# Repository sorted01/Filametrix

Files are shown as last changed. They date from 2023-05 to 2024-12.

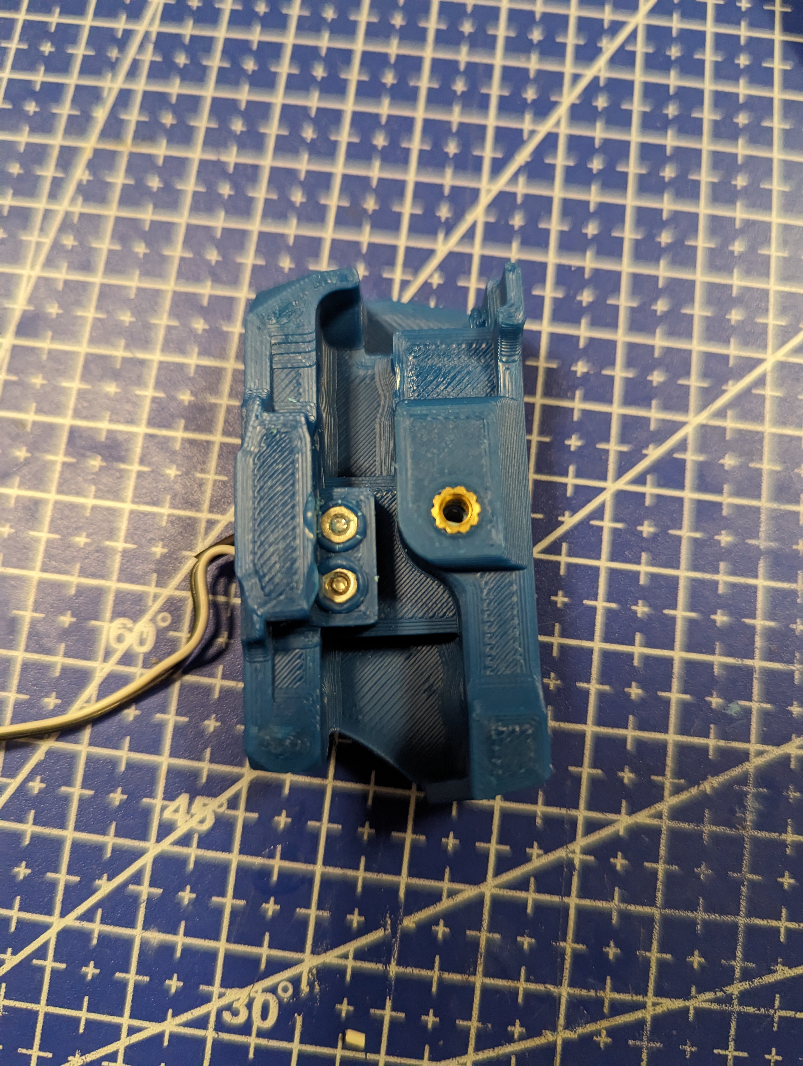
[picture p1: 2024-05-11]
STL/StealthOrbiter/PXL_20240206_062519943.jpg

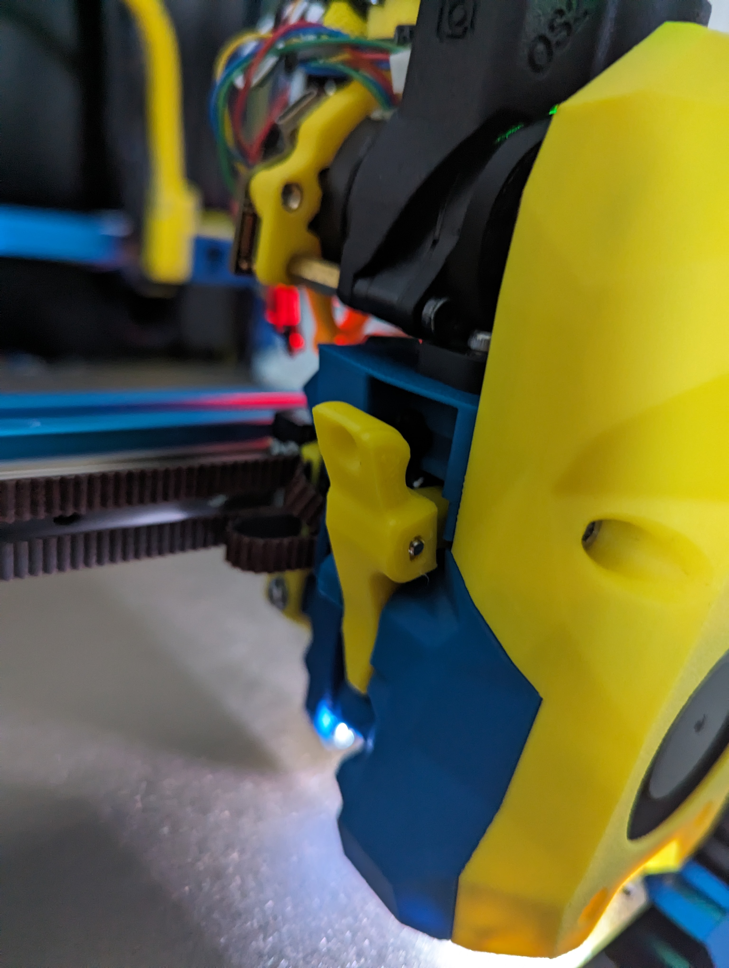
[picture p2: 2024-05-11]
STL/StealthOrbiter/PXL_20240206_194107226.jpg

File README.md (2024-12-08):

# Filametrix Mod


This is a mod of the Voron Stealthburner which adds a filament cutting possibility!




### Main Body
#### Main Body for old motor plate of Clockwork2
- SB_CW2_Main_Body_Cutting_with_2xD2F_ECAS
- SB_CW2_Main_Body_Cutting_with_D2F_ECAS
- SB_CS2_Main_Body_EBB_ECAS_D2F "CW2 main body for the ERCF w/ ECAs, bearing switch, and SB2209 Canbus mods" Thanks to [juliusjj25](https://github.com/juliusjj25)

#### Main Body for new motor plate of Clockwork2
Adapting to recent changes in the Clockwork2 design (July 2023) - Left new / Right old
grafik

A step with file the material removed of the motor plate is available here [Cutoff new motor plate](https://github.com/sorted01/Filametrix/blob/main/CAD/CW2_new_motor_plate/SB_CW2_cutoff_new_motor_plate.stp)

*Not all main bodys are converted yet. Use the old [motor plate](https://github.com/sorted01/Filametrix/blob/main/STL/motor_plate.stl) if your main body is not listed below.*

A more compact version using a M6 bowden fitting instead of the ECAS is also available for some main bodys. 
Additonally, a more rigid [latch](https://github.com/sorted01/Filametrix/blob/main/STL/[a]_latch_M6.stl) is available for the M6 version. (ECAS version of the latch is compatible with all M6 main bodys.)

* ECAS mount
	- SB_CW2_new_motor_plate_Main_Buddy_Cutting_with_ECAS

* M6 bowden mount
	- SB_CW2_new_motor_plate_Main_Buddy_Cutting_with_M6

#### Support for LGX Lite
https://www.printables.com/de/model/576122-lgx-lite-stealthburner-filament-cutter

tommorox234 has created the main body for the LGX Lite. Feel free to get in contact with him via printables.
Thank you :)

#### Support for StealthOrbiter
- ORBITERMOUNT_STANDARD_PG7_V2_Cutting

by [emjay276](https://github.com/emjay276)

### Printhead
#### Update for Phaetus Dragon UHF and Phaetus Dragon UHF mini
- SB_Dragon_UHF_cutting_TH_Front or SB_Dragon_UHF_mini_cutting_TH_Front
- SB_Dragon_UHF_cutting_TH_Rear or SB_Dragon_UHF_mini_cutting_TH_Rear
- Knife_holder_Dragon_UHF

by [emjay276](https://github.com/emjay276)

#### Update for Bambu Hotend has been added.
- SB_Bambu_cutting_Printhead_back
- SB_Bambu_cutting_Printhead_front or SB_Bambu_cutting_Printhead_front_2
- Bambu_Adapter

Thanks to "Jakub Kadlec" from Facebook :) 

#### Update for Voron Revo Hotend 
- SB_RevoVoron_back
- SB_RevoVoron_front

by Russell Gower - NOTE currently untested!!

#### Update for Rapido Hotend

- see folder

say thank you to [juliusjj25](https://github.com/juliusjj25)  :) 

#### Update for Slice engingeering mosquito hotend

https://www.printables.com/de/model/614813-filametrix-mod-for-slice-engingeering-mosquito-hot

say thank you to "https://www.printables.com/de/@MakeAUsername_285162"

#### Update for Revo Micro
- SB_RevoMicro_back
- SB_RevoMicro_front

by Leif Lang - NOTE: Remixed from the Official Stealthburner and the remixed version for the Revo Voron by Russel Gower

## Motivation
I was looking at the ERCF MMU for several month now. What always kept me from starting the project were the discussions about issues and problems with  filament tip forming. Suddenly a new company showed us how they do it quite reliable. They just cut the filament. Further motivated and inspired by the design of @pure100kim who has built the [ERCF_Filament_Cutting_MOD](https://github.com/pure100kim/ERCF_Filament_Cutting_MOD) I started to build my own version of it.

## See how it works

Proof of concept 1: https://youtube.com/shorts/HOMG8cVk_U4

Proof of concept 2: https://youtu.be/tTcrxttyths

Filametrix in action: https://www.youtube.com/watch?v=tfMZWQRqtvY

## Good to know

Please be aware:
- We will need to use one of the ADXL mounting threads
- Depending on the setup and position of the cutting point we will most probably not lose any build volume
- For the main body i remixed the ECAS version from [Alexanderor](https://www.printables.com/de/model/433797-clockwork-2-ecas-fitting-for-ercf)

## What you need
### Print list
#### Toolhead
- 1x SB (hotend name) cutting Printhead back
- 1x SB (hotend name) cutting Printhead front
- 1x SB Main body Cutting with ECAS (or with sensor)
- 1x SB motor plate (as Stealthburner has seen a small update the newest plate does not fit anymore. So please use the one from this git)
- 1x SB latch ECAS
- 1x Cutting arm
- 1x Knife holder

#### Cutting point on gantry
- 1x depressor mount
- 1x depressor

#### Cutting point on gantry with servo
- tbd...

### Parts list - considering you already have a Stealthburner with Dragon Hotend

#### Toolhead: 
- Loctite
- 1x M3 nut (DIN934; ideally a countersunk tool to modify the nut for proper filament insertion)
- 2x M3 washer (0.5mm)
- 1x M3x18 SHCS (it repleaces the top left M3x25 SHCS from the SB-Cover mount) 
- 2x Voron heat inserts
- 1x M3x18 FHCS (counter sunk screw)
- 1x M3x8 SHCS
- 1x M2.5x16 SHCS (15-18mm works)
- Spring 0.4x4x15 or alternative of ballpoint pen (L=15mm; D<=4,5mm) (I've ordered some for testing, to have a "defined" spring)
- Type 4 metal hobby blades (we will cut it to length) [Link](https://de.aliexpress.com/item/1005005117830095.html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) Amazon link, these need glue to be held in but work fine (USA) [Link](https://www.amazon.com/dp/B07QP8L1QG)
- 

#### Cutting point on gantry
- 1x M3x16 BHCS
- 1x M3 nut
- 1x M3x8 FHCS
- 2x M3 SHCS (Lengths: 6mm - no backers, 10mm - titanium backers, 12mm - MGN9 rails)
- 2x Voron heat inserts

## Assembly
### Cutting arm
#### Cut skalpel to length l=26mm

##### Result

#### Insert skalpel into knife holder
Insert the skalpel (which is cut to 26mm) into the knife holder until you see it in the little hole. Use pliers to push it into the knife holder. Some force should be needed as the skalpel should stay in place due to the "pressfit". If that's not the case add some glue.(Depelding on skalpel tolerances)

#### Put knife holder into cutting arm
The M2.5x15 screw is directly screwed into the plastic of the knife holder. The tip of the screw should be flush with the cutting arm or no more than 0.1-0.3mm above it.
Check the orientation of the hole for the M2.5 screw in the knife holder. It needs to be on the bottom side.

**!! The knife holder must move up and down without friction in the cutting arm but shoult not have a lot play. Maybe some grinding is needed. !!**




### Add heat inserts

Tip here for the heat set that goes above the cutter I would suggest drilling the threads out with a ~2.5mm drill bit. On the hotend holder side below the cutter make sure you flare out the PTFE tube to help guide the filament.
#### Main body

#### SB cutting Printhead back

#### Depressor - one on either end, end with ribs should be flush with surface below ribs with no plastic sticking up past surface


#### Finished cutting point assembly should look like this
Note: for titanium backers, the backer should be centered between belt clamps and the end of the depressor mount should be flush with the end of the backer. This will work for all backers with 10/20/40mm spacing with the furthest back hole 5-15mm from the end. Height of depressor should be adjusted to press in the depression on the cutting arm and the BHCS can be adjusted in and out for the right positioning and locked in place with the M3 nut.
261054978-7247e729-06e5-4cba-a8ad-aafa2b9bd7a1

I need some time to finalize assembly instructions. If you have questions you'll find me in discord "sorted#8941"

## Code

**The code only works with https://github.com/moggieuk/Happy-Hare** If you haven't updated yet you really should.

Latest version provided by [thisiscam](https://github.com/thisiscam)

I added the option to push the filament tip back into the hotend

Copy additional.cfg to your printer config directory and include it in your printer.cfg below all of the mmu includes via [include additional.cfg]

### In mmu_parameters.cfg:
set form_tip_macro: _MMU_CUT_TIP

set toolhead_extruder_to_nozzle and toolhead_sensor_to_nozzle to corresponding measured values of your toolhead.

set force_form_tip_standalone: 1

### In additonal.cfg
You will need to adjust the parameters in addtional as well, like setting up your cutter location, speeds, etc. More information in the cfg file itself.
set variable_output_park_pos: ... to the distance from the nozzle tip to the blade

#### Servo
If you are using a gantry servo, remove the hashtags related to "gantry_servo"s in this file.

# If you want to support me

paypal (https://www.paypal.com/paypalme/sorted01)

#### Optional Next location
The _MMU_CUT_TIP now has an option to move to a "next location" immediately after making the cut. For instance,  set it to the purge tower's location from the slicer. The _SET_LOC_AFTER_TOOLCHANGE sets this location, and the _MMU_CUT_TIP macro will be responsible for traveling immediately after the cut but prior to the unload. See the orcaslicer's toolchange gcode two messages down as an example. If you don't plan to use it, it's safe to ignore this point.


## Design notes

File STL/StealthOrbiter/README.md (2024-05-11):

Remixes below bt SaltyPaws have been tested (see attached images) with lever arm from https://www.printables.com/model/647601-orbiter-filametrix-mod.

Cutting remix by SaltyPaws using latest from https://github.com/sneakytreesnake/StealthOrbiter for mounting CANBUS or those who don't need PG7 and need their lever arm to work.

**ORBITERMOUNT_No_Sensor_V3_Cutting v2.stl**

Cutting remix by SaltyPaws no sensor version.

**ORBITERMOUNT_Sensor_V3_Cutting v2.stl**

Cutting remix by SaltyPaws as above, but now with slot for below extruder filament sensor. Note that this needs to be printed with supports painted on for the sensor section, as bridging is not sufficient here. Sensor version uses v0.1 BOM limit switches (lever microswitch) with the end of the lever trimmed to fit. It uses the metal ball from the orbitor sensor (6 mm). M2 hex bolts can be threaded straight into the plastic, or you can melt a m2 nut on the other side.

Below remixes by Charles@CharlesDahlma_340167 (https://www.printables.com/model/647601-orbiter-filametrix-mod.)

**Cutter body small.obj**
Used with all model files above

**Orbiter body Filamentrix.obj**
PG7 version

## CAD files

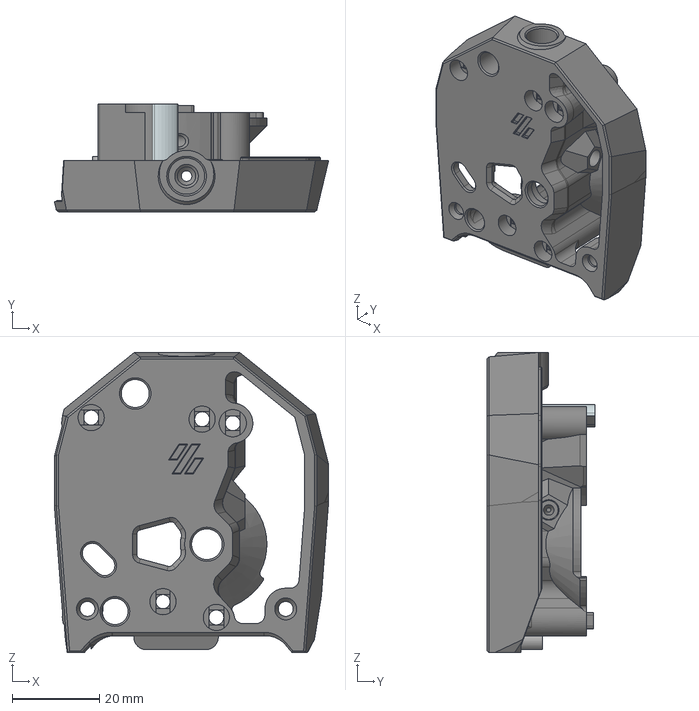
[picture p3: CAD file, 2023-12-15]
CAD/CW2_new_motor_plate/SB_CW2_new_motor_plate_Main_Buddy_Cutting_with_ECAS.stp
62.8 x 24.7 x 68.7 mm

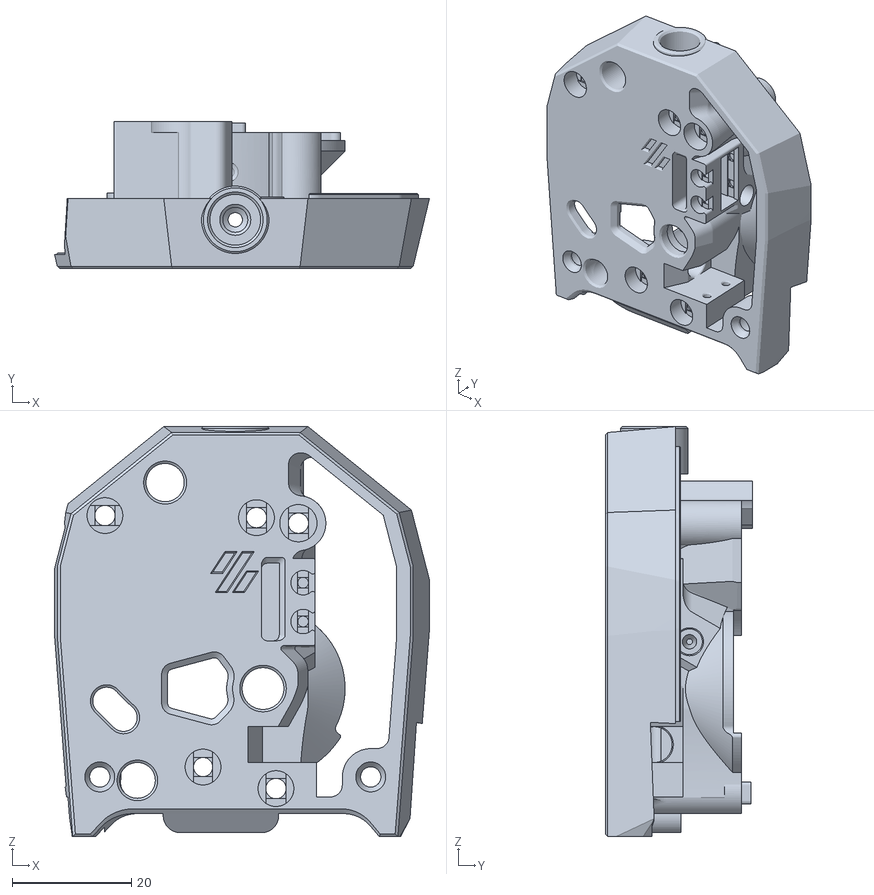
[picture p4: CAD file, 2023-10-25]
STL/SB_CW2_Main_Buddy_Cutting_with_2xD2F_ECAS fix Rev1.stl
62.8 x 24.7 x 68.7

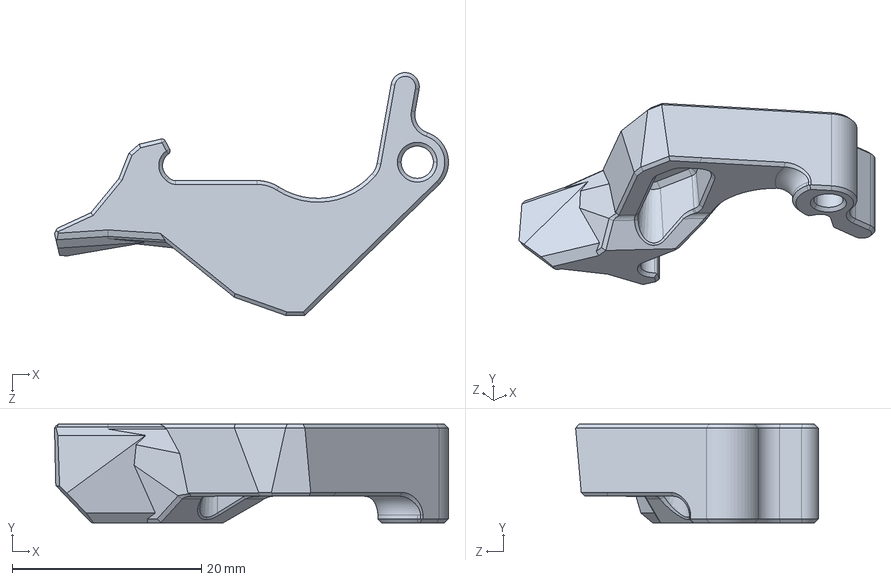
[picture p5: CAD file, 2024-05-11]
CAD/[a]_latch_ecas.STEP
41.6 x 10.4 x 25.6 mm

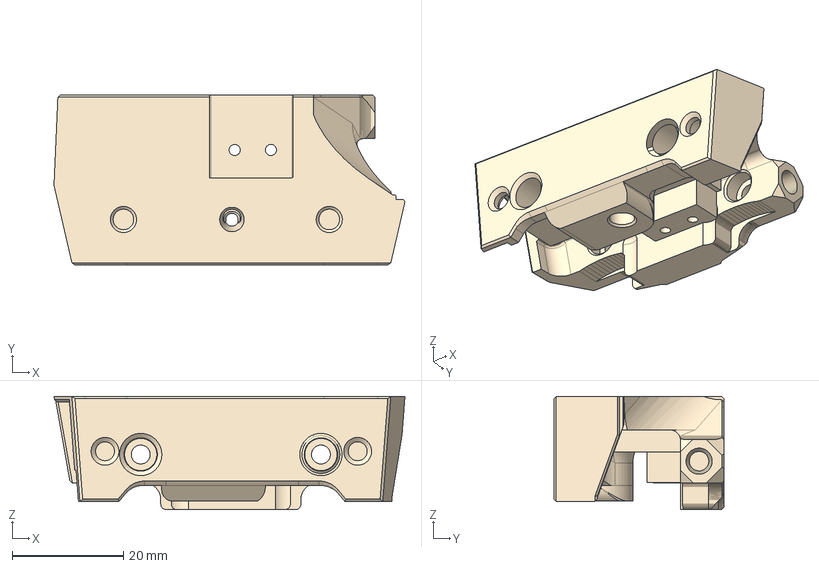
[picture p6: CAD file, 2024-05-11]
CAD/StealthOrbiter/ORBITERMOUNT_Sensor_V3_Cutting v2.step
63.1 x 30.6 x 20.4 mm

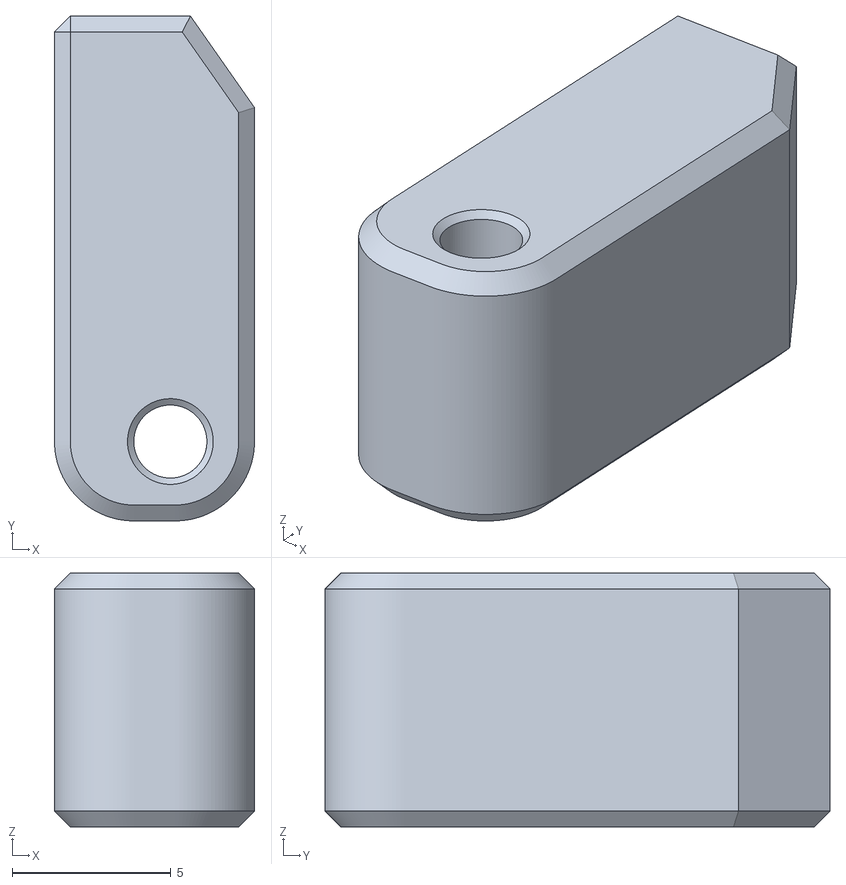
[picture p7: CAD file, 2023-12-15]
STL/Dragon UHF (mini)/Knife_holder_Dragon_UHF.stl
6.30 x 15.9 x 8.00

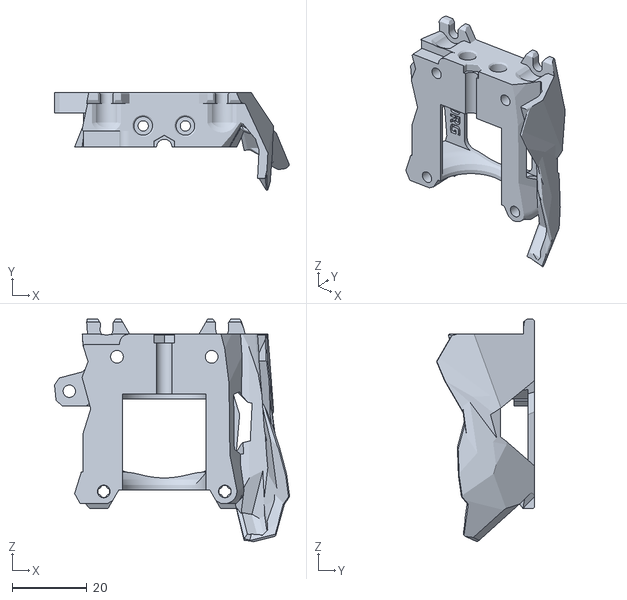
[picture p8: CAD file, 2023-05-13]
STL/Dragon/SB_Dragon_cutting_Printhead_front.stl
63.0 x 26.3 x 59.7

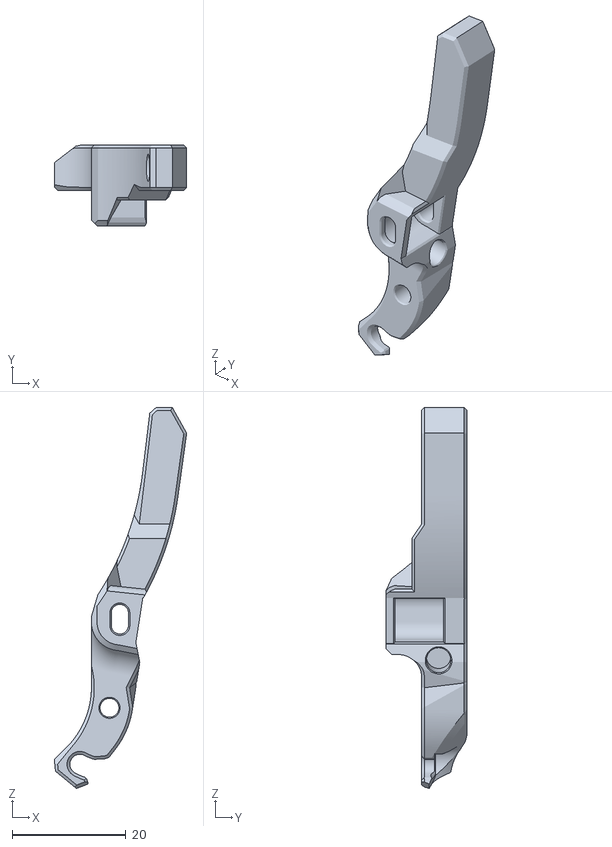
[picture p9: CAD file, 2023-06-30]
STL/more_travel/[a]_Cutting_Arm_MT_Rev00.stl
23.3 x 14.2 x 66.9

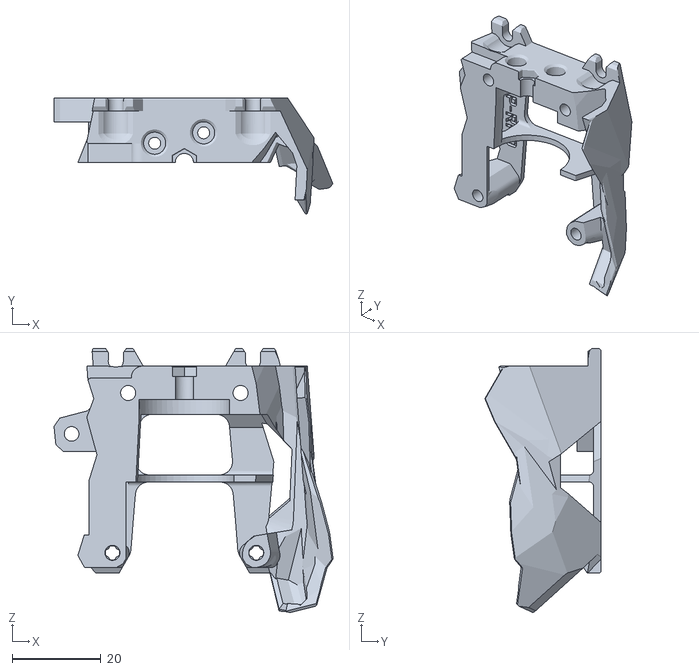
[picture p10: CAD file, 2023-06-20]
STL/Rapido/SBRapido TH Rear CW2_cutter.stl
63.0 x 26.3 x 59.7

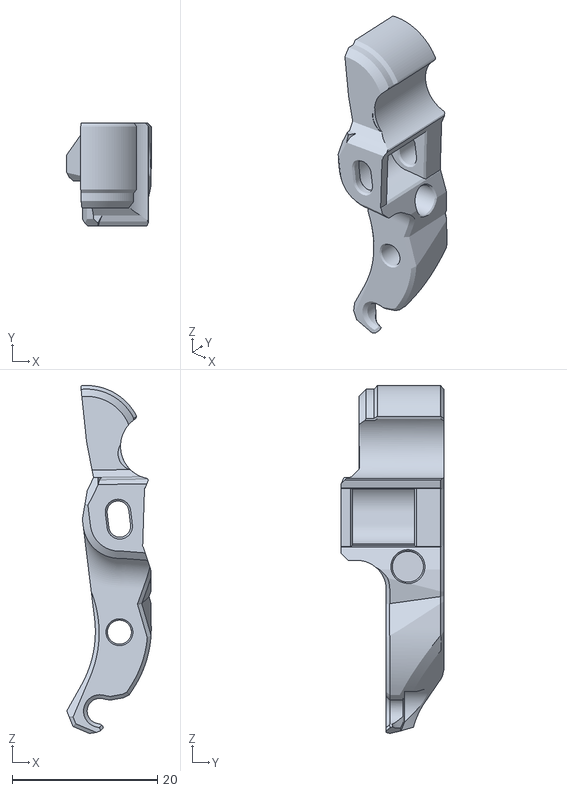
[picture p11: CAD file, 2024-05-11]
STL/StealthOrbiter/Cutter body small.obj
11.6 x 14.2 x 48.0

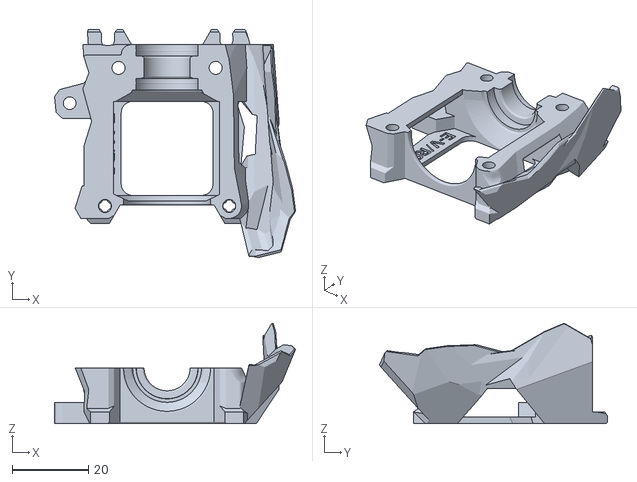
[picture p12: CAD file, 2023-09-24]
STL/V6 R6/SB_V6_R6_cutting_printhead_back.stl
63.0 x 59.7 x 26.3

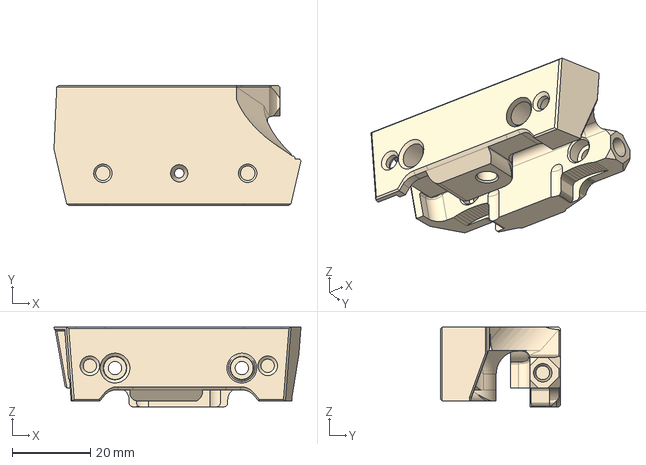
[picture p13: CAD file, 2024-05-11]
CAD/StealthOrbiter/ORBITERMOUNT_No_Sensor_V3_Cutting v2.stl.step
63.1 x 30.6 x 20.4 mm

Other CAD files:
CAD/CW2_new_motor_plate/SB_CW2_new_motor_plate_Main_Buddy_Cutting_with_M6.stp
STL/SB_CW2_Main_Buddy_Cutting_with_D2F_ECAS.stl
STL/SB_CW2_Main_Buddy_Cutting_with_ECAS.stl
STL/[a]_latch_ecas-new_motor.STL
STL/Revo/SB_RevoVoron_back.stl
STL/Revo_Micro/SB_RevoMicro_back.stl
CAD/[a]_latch_M6.stp
CAD/CW2_new_motor_plate/SB_CW2_cutoff_new_motor_plate.stp
CAD/CW2_old_motor_plate/SB_CW2_Main_Buddy_Cutting_with_ECAS.stp
CAD/Cutting_Arm.stp
CAD/Knife_holder.stp
CAD/Knife_holder_Dragon_UHF.stp
CAD/SBRapido TH Front_cutter.stp
CAD/SBRapido TH Rear CW2_cutter.stl.stp
CAD/SB_Dragon_UHF_cutting_TH_Rear.stp
CAD/SB_Dragon_UHF_mini_cutting_TH_Rear.stp
CAD/SB_Dragon_cutting_Printhead_back.stp
CAD/SB_Dragon_cutting_Printhead_front.stp
CAD/SB_RevoVoron_back.stp
CAD/SB_V6_R6_cutting_printhead_back.step
CAD/StealthOrbiter/ORBITERMOUNT_No_Sensor_V3_Cutting v2.stl.f3d
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

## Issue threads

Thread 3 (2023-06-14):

Stealthburner Rapido Uhf

gogsi1, 2023-06-14:
do it under rapido uhf

gogsi1, 2023-06-14:
> Sorry, I don't get it? :)

Make your mod for this version https://www.teamfdm.com/files/file/631-stealthburner-rapido-uhf/

sorted01, 2023-06-20:
[@juliusjj25](https://github.com/juliusjj25) has created it for Rapido. Don't know if it is same as UHF. Please check the updated files and let me know.

gogsi1, 2023-06-20:
> [@juliusjj25](https://github.com/juliusjj25) has created it for Rapido. Don't know if it is same as UHF. Please check the updated files and let me know.

Thanks, this is the Rapido HF version. It remains to be done for UHF, but here only the airflow needs to be lengthened.

gogsi1, 2023-06-20:
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

dridas, 2023-06-21:
I actually started modifying this yesterday for the Rapido UHF.  You actually need to modify the SBRapidi TH front cutter, to add the third hole for the pivot point.  I managed to get that done yesterday, but the cutter arm isn't long enough.

I took the stealthburner rapido uhf and just overlaid the differences and it seems to work for that part.  I need to extend the arm above the spring so it lines up with where the blade lays down on it.  Work in progress, and will attempt to do that this evening.

One question, has anybody thought about using N52 5x3mm opposing magnets instead of the spring?

gogsi1, 2023-06-21:
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

Hmm, good idea about the magnet. Can you make a 6x3 mm size?

dridas, 2023-06-21:
I was inclined to use the 6x3 magnets at first, since they seem to be more common.  The cutter arm is pretty narrow, and just barely fits a 5mm magnet. On second review, it looks like I didn't make the cutout for the knife cutter on the arm, so might not have to adjust the cutter arm after all, but will need to make another print of the Rapido UHF Front Cutter.

I'll see what I can do about the 6mm magnet. Hope to have a finished prototype by the weekend, but life might get in the way. I have lots of magnets sitting around, and even some 6x10mm's that I think would be better for the body side to provide a stronger repel of the cutter arm.  I'll start with 6x3's, and see hot that works first

sorted01, 2023-06-21:
Good idea with the magnets. Somehow I always had the spring in mind. Thanks for modding the parts. Currently I can hardly find time. Family and stuff 😅🙈

dridas, 2023-06-21:
Prototype printing now, with 6x3 magnets. Running it a little slow, cause I'm a little sketchy on overhangs, but give it a few hours, and hopefully I'll know if it's doable.  Got some life things to deal with in the mean time, but more to follow.

dridas, 2023-06-22:
I can't make any gaurantees that this is 100% correct, or that it couldn't be made better. Still a work in progress, and I haven't mounted my Rapido UHF to it (yet).

I did have to adjust the M3 heatset inserts, since they were slipping a little once I set them in place. Just the two that mate with the back of the Rapido (where the 6mm magnet goes).  If you make any modifications, I'd appreciate a message, since obviously any improvements might be good for the community.

[https://github.com/dridas/SBRapido-UHF-Cutter](url)

also, credit to Filametrix, and this repo, and any contributors. I didn't do any of these designs myself, just made some slight modifications and blended stl's.

gogsi1, 2023-06-23:
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

When can I download your version? I really want to try it.

dridas, 2023-06-23:
For some reason the link didn't work.
Try This one:

https://github.com/dridas/SBRapido-UHF-Cutter

gogsi1, 2023-06-23:
> For some reason the link didn't work. Try This one:
>
> https://github.com/dridas/SBRapido-UHF-Cutter

Thank you, the link is working now.

BlackNet, 2023-08-15:
>

Do you have any videos of the magnets in use?  Also am going to print this and see. I have been trying to make some mods for the UHF but have yet to be happy with what I have done with them.  It looks like this one should work just fine for me.

Closed 2023-09-07.

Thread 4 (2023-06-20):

Rapido CAD/STL

juliusjj25, 2023-06-20:
Not an issue, but I took your CAD modifications and applied them to the Rapido Toolhead design and created the CW2 main body for the ERCF w/ ECAs, bearing switch, and SB2209 Canbus mods

@CheeseFrog V2.4559

[Rapido & SB2209.zip](https://github.com/sorted01/Filametrix/files/11795457/Rapido.SB2209.zip)

sorted01, 2023-06-20:
Thank you so much! :) I've added it to the files and updated the readme. I hope this is fine!

I would close the "not an issue" :D

akillmer, 2023-06-23:
@juliusjj25 Which PCB cover are you using for this? The original cover leaves a considerable gap.

juliusjj25, 2023-06-24:
@akillmer I am using the one from the BTT SB2209 design on Github
 https://github.com/bigtreetech/EBB/blob/master/EBB%20SB2240_2209%20CAN/Custom%20Printed%20Parts/cable_door_EBB_SB.stl

jgorges7, 2023-08-14:
@juliusjj25 Does this use a 5.5mm ball bearing for the sensor? Better yet, do you have a step file for the main body? I do not intend to use the filament sensor and would like to remove the added resistance from the system. Thanks!

juliusjj25, 2023-08-14:
> @juliusjj25 Does this use a 5.5mm ball bearing for the filament sensor? Better yet, do you have a step file for the main body? I do not intend to use the filament sensor and would like to remove the added resistance from the system. Thanks!

This uses the 7mm bearing ball from the ERCF usermods. I appear to have misplaced the step file for these mods.

Closed 2023-06-20.

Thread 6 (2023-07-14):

Is it v6 compatible?

FrAn3030, 2023-07-14:
Hi i would like to us your mód with normal v6

FrAn3030, 2023-07-15:
is there any chance too make a v6 mount or is it compatible with revo?

Heiliger-Gral, 2023-08-22:
> is there any chance too make a v6 mount or is it compatible with revo?

you mean for Groove-Mount .. I'm looking for something like that right now :)

sorted01, 2023-09-07:
As the hotend is to high for this design I don't think so. You can check the "motivation" text. There I've linked a design which uses the V6 hotend

Closed 2023-09-07.

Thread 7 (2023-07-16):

The dual D2F SB part has a major flaw

scottgrim, 2023-07-16:
When the part for the heat insert was added at the exit path of the CW2 the entire filament path between the last sensor and the insert was not reduced to 2mm so there's a lip inside the part for filament that has any amount of curl to catch on.

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

That circled section should be 2mm straight through.

scottgrim, 2023-07-16:
Something like this which I just hacked together in TC real quick.
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

sorted01, 2023-10-09:
Sorry, missed that one. You're right. As i did not design this part and i have no step i'll delete it for now. Could you share your "quickfix"?

sorted01, 2023-11-06:
It's solved :)

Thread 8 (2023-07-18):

Crazy Dragon (Dragon UHF mini mode)

messymouse, 2023-07-18:
I would love a version for Crazy Dragon, which is a Dragon UHF without the nozzle extender part on it. Crazy Dragon mount can be found here- https://github.com/VoronDesign/VoronUsers/tree/master/printer_mods/eamars/stealthburner_crazy_dragon_toolhead/STL

Its basically a combination of Rapido and Dragon, which are both already created here, I just have no idea how to do the 3D modeling to merge them correctly. Thanks!

ntsanov, 2023-07-24:
I'm using crazy dragon, basically a Phaetus Dragon SF with a Mellow Crazy Volcano block. I'm also interested. Since the step files for the Crazy Dragon are released it should be straight forward. I might do it myself when I get to the ERCF at some point in the following months

messymouse, 2023-07-27:
I don't know anything about 3D modeling, and every time I have tried figuring out how to use a step file it was a headache and I got no where. This seems like a simple thing to throw together for people who know what they are doing, and I would greatly appreciate it!

EmJay276, 2023-12-14:
I just added versions for the Phaetus Dragon UHF and Phaetus Dragon UHF mini :)
https://github.com/sorted01/Filametrix/pull/36

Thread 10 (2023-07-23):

Bondtech LGX lite // Canbus // ball bearing filament sensor

ricosander, 2023-07-23:
I like the idea of cutting the filament, b/c I already ran into problems with the sensor and the tip finding its way there.
If not planned already, could you add support for the bondtech lgx lite?
Maybe the ball bearing filament sensor could be optional, with the cutting feature it should not be a problem anyway.

I guess the lgx lite is widely used along with the Canbus 2209.

sorted01, 2023-09-08:
https://www.printables.com/de/model/576122-lgx-lite-stealthburner-filament-cutter

Closed 2023-07-23.

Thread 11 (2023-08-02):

Solution for the gantry mounted part for people with extrusion backers?

erazor666, 2023-08-02:
any ideas on how to attach the gantry part of the cutter mod when you have  extrusion backers on your Y axis?
I really want to keep them and use this mod :(

o1hitman1o, 2023-08-03:
I would say is it possible to put the backers on the exterior side instead of the top? I don't have the backers installed myself but if it will fit I would think on the side would offer the same performance at on the top.

erazor666, 2023-08-07:
I would think the backers will not have the optimum performance of counteracting the bi-metallic effect that they are there for :) I guess that it is quite possible to design something in Fusion360 when I get a free minute. Was just looking for the possibility that someone else had this same issue :)

erazor666, 2023-08-15:
I guess people have different backers, I myself am using the rails of my old MGN9's that used to be on my V2 X axis. since they were rather useless after converting to MGN12 on the X rail. There are some premade backers that are titanium and such, dont know if they have same screw hole pattern as a MGN rail. What are you basing the design on? From a purely visual standoint this seems very much the way to go. (and the way I was doing it on my napkin design ) :)

juliusjj25, 2023-08-16:
It's my own design from scratch, I have titanium backers that I am
designing around but I do not have them installed yet, which is why I was
wondering about the positioning. The titanium backers have 40mm hole
spacing and they have varied distances from the edge of the backer 5-20mm
based on the build size. I do not know the hole spacing on the MGN9 rails
and that may or may not be standard across rails. If it helps, when I
finish the design I could share the step or native Solidworks file for you
to modify to your needs, likely you would just need to change the
overall height and the hole spacing and relationship to the edge.

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

juliusjj25, 2023-08-16:
I took some measurements and figured it out and adjusted the CAD. I had to make it wider because the backer hole aligned under the 2020 piece. I also made a 250, 300 & 350 build version. Here is the 300 version.
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

SLDPRT, STEP & STL files attached. :) Print/modify at your own risk, I have not done any sort of testing or printing of any of this yet. I am waiting on parts to build this up along with several other mods, so I won't get around to testing for several weeks.
[2020_mounts_ti_backer.zip](https://github.com/sorted01/Filametrix/files/12354111/2020_mounts_ti_backer.zip)

erazor666, 2023-08-16:
I will have a look at this in the afternoon, it looks like the way to go very much. Hole spacing on a MGN9 is 20mm it seems from measuring. Probably this would be worthwhile to do a pull request on eventually, there are many people who use backers (and should)

juliusjj25, 2023-08-16:
If your hole spacing is 20mm then this should work for you as well.

I printed one of these last night since my printer wasn't running, I have some tweaks to make before I'd say this is ready to go. The t-slot profile needs more clearance and I want to tighten up the holes at the top because the screws don't quite bite enough to my liking, maybe add a gusset or to to stiffen it up.

I might design a full 3D printed part to make this a little cleaner, I am not sure how much force it takes, but given the lever arm thickness, it can't be that much.

I'll see where I get on this today, I think it will still need a build size variant of each unless I make it slotted with some notches to align the screws to.

juliusjj25, 2023-08-16:
This is what I have come up with this morning as a 2 piece design. The mount spacing is 40mm and it has 10mm slots, so it can be adjusted front to back 5mm from nominal, which is the difference between the 250, 300 & 350 build sizes. For titanium backers, it should be aligned with the back of the backer. The BHCS is an M3x16mm and is adjustable in and out with a nut to lock it in place and depress the lever, this could be SHCS as well, I just like the idea of a rounded head to interface. The screw mounting the two pieces is an M3x8mm FHCS and it's in a slot and adjustable up and down. The two pieces have grooves to index together to prevent movement and are adjustable in 2.4mm increments, so the farthest you could align from perfect would be 1.2mm, this seemed a reasonable tradeoff between keeping standard 0.4mm nozzle settings and requiring a finer nozzle to print the parts. For 3mm backers this uses M3x10mm SHCSs, for thicker backers like MGN9 rails, you'll have to compensate for the thickness with a longer screw.
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

I will try to print these tonight when I get home to see how they do in both printability and interfacing with each other and my backer, but will not be able to test with the actual filament cutter for several weeks. I will confirm they at least interface together and with the backer and then upload part files if they do and you're welcome to test them after that.

erazor666, 2023-08-16:
Awesome, that is much cooler than any design I would have come up with. Absolutely a PR worthy. :)

juliusjj25, 2023-08-17:
Here it is set in place, not actually mounted but just set where it would go. I adjusted the height to the original 40mm of the 2020 extrusion so this could work with or without backers, MGN9 backers could work as long as the hole spacing is 10/20/40mm and the first hole is 5-15mm from the back edge.
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
[depressor.zip](https://github.com/sorted01/Filametrix/files/12370989/depressor.zip)

juliusjj25, 2023-08-17:
If you want to print these, you'll need to reorient them to this position. The standard orientation of the axes between SS and Solidworks are different.... I need to figure out which way to model in Solidworks to get them to orient correctly in SS. I'll fix it for a final model.
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

juliusjj25, 2023-08-17:
I created a pull request, I'll admit, I have no clue if I did it right though!

shaneshort, 2023-08-26:
looks like this has been merged, should be ok to close the issue?

sorted01, 2023-08-26:
I merged it. Sorry was out for some time due to my baby 👶

Closed 2023-09-07.

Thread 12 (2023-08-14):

Will an 18mm spring work?

juliusjj25, 2023-08-14:
https://www.amazon.com/dp/B0BHHZBPW9/
https://www.amazon.com/dp/B089JYV7BT/

jfryman, 2023-09-07:
@juliusjj25 I tried out the [latter link](https://www.amazon.com/dp/B089JYV7BT/) last night, and had no luck with it as-is. The spring was just too long and fully compressed the knife wouldn't fully cut. I ended up trying to cut _only_ one side of the compressed end to some success.

The [first link](https://www.amazon.com/dp/B0BHHZBPW9/) won't arrive for me until Sunday, but I expect similar behaviors.

I'm also looking for a spring that might work better I can source from somewhere other than a pen spring (because that also seems unclear to me what sort of pen I should try and source this from).

juliusjj25, 2023-09-08:
I ended up ordering the second link and it is working just fine for me, however the hole for the spring is so tight it takes some work to get in in correctly.

jfryman, 2023-09-09:
Agreed. I had a similar issue and ended up grinding out just the slightest amount space to get the spring to seat. Very snug. It still wasn't as good as I hoped, and on a random shot I just bought this:

https://www.amazon.com/dp/B08169QK5X?psc=1&ref=ppx_yo2ov_dt_b_product_details

The spring for this is longer than requested (around 26mm) but it has the right amount of tension to have it spring right back in the way I'd expect.

juliusjj25, 2023-09-09:
It would be good at some point to have this design modified around a more commonly available spring geometry since this seems to be a pain point finding the right spring.

sorted01, 2023-09-09:
I have some springs lying around. Just need to find some time. Sorry 😣 will keep you posted

EmJay276, 2023-12-14:
> It would be good at some point to have this design modified around a more commonly available spring geometry since this seems to be a pain point finding the right spring.

I enlarged the hole for the spring in my design to 5mm and use a 5x0.4x30 [Spring](https://www.aliexpress.com/item/1005002652972568.html), I also use for my bowden tubes to prevent kinking.

Works perfectly fine for me, it's just a little bit difficult to get it in place at first.
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

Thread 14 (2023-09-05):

Happy Hare Update

drecoor, 2023-09-05:
Happy Hare seems to have updated I think, and the provided gcodes aren't working anymore. It looks like ercf_software.cfg was replaced with mmu_software.cfg, and there is no variable_standalone option anymore. The ercf_additional.cfg file is not working with the update as well.

sorted01, 2023-09-05:
Thank you for the hint. Was expecting that. Unfortunately I currently have no time to take a look on how to fix it. This will take a few weeks. (2-3). Sorry for that. If someone can check it earlier I will update the GitHub

Closed 2023-09-16.

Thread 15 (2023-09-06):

Which CW2 motor plate to use?

JAMMnGA, 2023-09-06:
I printed your EBB main body and the current CW2 motor plate at VoronDesign.  The  top alignment tab on the main body does not match the recess on the motor plate.  Which motor plate should I use?

sorted01, 2023-09-07:
I got pinged in discord regarding that topic. Can you share a screenshot? I will try to update

sorted01, 2023-09-07:
Stealthburner has seen a small update from Voron team. Due to that the motor plate doesn't fit anymore. I've uploaded the motor plate you need for filametrix. These parts will flush together again.

Closed 2023-09-07.

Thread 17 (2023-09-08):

Build Volume Collision

juliusjj25, 2023-09-08:
How do you prevent the toolhead from colliding with the gantry mounted cutting point? It appears there is about a 50mm(Y) by 25mm(X) square in the back left corner where the toolhead could collide with the depressor.

gennro, 2023-09-09:
I would probably put your corner in the front left of your printer so it doesn't collide during homing operations and make sure none of of bed leveling etc go into that corner. Orcaslicer supports bed exclude zones as well along with nozzle volume purge compensation for handling the cut off piece of filament in the nozzle during a swap.

appleimperio, 2023-09-11:
@juliusjj25 I'm sorry to hack this post. Can you make a CW2 main buddy EBB SB2209 but without any sensor? just the ECAS. Thanks

juliusjj25, 2023-09-11:
> I would probably put your corner in the front left of your printer so it doesn't collide during homing operations and make sure none of of bed leveling etc go into that corner. Orcaslicer supports bed exclude zones as well along with nozzle volume purge compensation for handling the cut off piece of filament in the nozzle during a swap.

I figured it out, I created an STL of the bed with the corner notched out and uploaded that as my custom bed in SuperSlicer, now it won't let me place anything in that spot.
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

Now I'll just need to change QGL and bed mesh to remove that corner as well.

juliusjj25, 2023-09-11:
Here is the STL for a 300mm bed, I had to zip it to be able to post it here.
[Notched Bed.zip](https://github.com/sorted01/Filametrix/files/12580070/Notched.Bed.zip)

LostFool, 2023-11-22:
> Here is the STL for a 300mm bed, I had to zip it to be able to post it here. [Notched Bed.zip](https://github.com/sorted01/Filametrix/files/12580070/Notched.Bed.zip)

How did you get it to accept an origin of 0,0 at bottom left corner? I am trying to do a 350mm variant and Prusaslicer only accepts a custom one with origin at center of bed.

juliusjj25, 2023-11-22:
I use Superslicer and it worked just fine 0,0 should be the bottom left corner?

LostFool, 2023-11-22:
Prusaslicer is just dumb then.

https://help.prusa3d.com/article/custom-bed-models_158431

I tried making the origin bottom left corner and I just get errors in prusaslicer.
Unfortunately I am stuck in Prusaslicer for the time being because I have a custom version that is more in-tune to purge temperatures of varying temperature filaments (PLA & ASA in same model)

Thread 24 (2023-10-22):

When using SB_CS2_Main_Buddy_EBB_ECAS_D2F big gap with default cable cover?

MaikelKelder, 2023-10-22:
Hi,

Not really an issue, but when using this SB_CS2_Main_Buddy_EBB_ECAS_D2F you leave a big gap open when using the default cable cover for the Stealthburner.
I wasnt able to find a adjusted one, I almost assume it exists?

Thanks for the MOD, its a beast! saving so much issues swapping filaments.

k5beason, 2023-11-07:
Same issue. Did you ever find the correct cover?

k5beason, 2023-11-08:
I believe the BTT files will work https://github.com/bigtreetech/EBB/blob/master/EBB%20SB2240_2209%20CAN/Custom%20Printed%20Parts/cable_door_EBB_SB.stl

MaikelKelder, 2023-11-08:
I will check it out, thx!

Op wo 8 nov 2023 om 03:02 schreef k5beason ***@***.***>

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

k5beason, 2023-11-08:
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

Let me know. On mine the bottom securing screw hole is about 1-2mm off still. I can't find any other covers that are close.

gabber130779, 2024-04-19:
same problem, but solved. I modified the cable door from BTT. you can fine it here.

https://www.printables.com/de/model/849383-cable-door-forstealthburner-cw2-filametrix-with-ec

MaikelKelder, 2024-04-19:
Thank you!!

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

gabber130779, 2024-04-24:
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

Did it fit now?

MaikelKelder, 2024-04-25:
No, doenst fit, I guess the version with a double sensor in there is thicker or so.
Im using the OLD version of the CW2 motor plates, because of that, double sensors.
It also has a cutout for the 2209 canbus on the bottom.
I guess I have to get creative to get one fitting ;-)
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

MaikelKelder, 2024-04-25:
I am going to try this body, also double sensor, but no cutout and sensor is screwed on from bottom, much better.
Lets see if I can find a door for that, otherwise, ill make one and post it.

MaikelKelder, 2024-04-25:
Ok, I jus tprinted and fitted these and they work together. Your cover also fits but the hole for the screw is only just out of place, 2mm or so.

Vented Cover:
https://www.printables.com/model/772880-ebb-sb22402209-vented-cable-door-jan-2024-update/files

double sensor CW2 plate:
https://www.printables.com/model/826480-filametrix-body-cw2-for-sb2209sb2240-with-dual-fil
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

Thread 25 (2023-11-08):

HGX large gear cw2 remix

Darkmadda, 2023-11-08:
I finished my filametrix remix. I picked up a large gear (HGX) and i remixed a mainbody created by someone else that adds a ecas/filament-sensor, now we have a model that works with filametrix. https://www.printables.com/model/641383-clockwork2-large-gear-hgx-ecas-ercf-filament-senso . The model is tested by myself but i'd welcome anyone else to print and test it. I really like the filament sensor in this model as it uses the actual gears to sense the filament so you know exactly when the filament is in a gripped position.

bartoszwas, 2023-11-22:
If You would like to make version for LGX Lite I'm eager to test.

Darkmadda, 2023-11-23:
There is a LGX version on the printables page. it is untested so i'd love to know if it works

bartoszwas, 2023-11-23:
If You mean this one: https://www.printables.com/pl/model/576122-lgx-lite-stealthburner-filament-cutter there's no filament sensor and lots of supports required to print it. No idea is it compatible with EBB SB22xx.

Darkmadda, 2023-11-23:
No use the links in my first comment.
https://www.printables.com/model/641383-clockwork2-large-gear-hgx-ecas-ercf-filament-senso
No sports required. Filament sensor built in look and the model it is remixed from to see how the sensor works. The sensor works a little different than other sensors but it does work and works very well

bartoszwas, 2023-11-23:
Ah, Ok. I didn’t notice that there’s also a LGX version. I’ll check that for sure.

Darkmadda, 2023-11-23:
as for the sb22xx board. i have a sb2209 but there isn't much room for it with the large gear installed so it is a really tight fit. But it does fit (may require a little finagling )

Darkmadda, 2023-11-23:
I just realized you want to use the whole lgx extruder. my design just uses the gear set from that. you won't be able to use the whole extruder just the large gears from it. if that is acceptable then go for it but if you are looking to use the prebuilt extruder than it wont. To use the the whole unit it would require me to remix the design you first linked to.

bartoszwas, 2023-11-23:
Yes I was looking for solution to use the whole extruder, but, hey, if I can use gears only and it’ll work then why not.

Darkmadda, 2023-11-23:
Please let me know how it works. The lgx version is untested

bartoszwas, 2023-11-23:
I will. Just need to get some time to print and assemble - at least on Sunday I'll be back with feedback.

bartoszwas, 2023-11-24:
Got some info.

LGX gear seems to be a lil bit off of the filament path.
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

Rest parts are printing, but for now no other issues. Will be back with info when I assembly it.

Darkmadda, 2023-11-27:
A few notes:
1. "LGX gear seems to be a lil bit off of the filament path. Picture doesn't show it good... IMHO it should be like 0.2 mm deeper."
- i'll look into adjusting that
2."I don't know how to install guilder. There's no hole for screw head... And IMHO a heat set insert would be nice there too"
-there shouldn't be a screw there it should be there should be a steel shaft that press fits in (it should have been in the gear set).
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
3. "Next is plastic sprocket axe - in main body the hole is much bigger then that steel pin?"
-there should be a bearing in there (again should have been in with the gears) is it possible for you to take a picture of all of the parts that came with your extruder (I know yours is not a gearset and is instead the kit so i don't know what you have) here is what my kit looks like
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
5. "Filament can stuck on main body exit"
-you are supposed to put a headset insert there (see breakaway here
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
6."Press fit parts doesn't fit so well."
 -I'll have to take mine apart and look at first picture. I know the part doesn't insert into the motor plate very far as for the second picture take the slot may be different from the latest CW2 release. they changed the shape of the motor plate slot. here in this picture
![Uploading IMG_20231126_223332.jpg…]()
(i know it's not of the large gear mod but it's extra parts i had laying around you can see that the slotted piece shape is much thinner on the left latest design. My remix is for the slightly older design so you will need the matching motor plate for that larger design) (i don't have a picture of the motor plate to show the actual slot). Make sure you are printing the correct motor plate. I'm guessing that is your problem. I've added the motor plates to the printables page so you can find them easier.

Darkmadda, 2023-11-27:
I just looked at the source design and the bearing i was talking about is a MR63ZZ bearing

bartoszwas, 2023-11-28:
So these are all parts I got from my lgx, three gears and three shafts.

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

According to filament exit If you make cross section view you will see that it’s before the jest set insert. There’s a relief inside of the model…

Could you please share step file of main body with sensor? On printables there’s only without sensor and scad I cannot open in fusion 360. I wanna make some modification and test but for couple of days I won’t have access to my pc

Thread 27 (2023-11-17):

Supporting Rapido UHF / Rapido 2?

dflemstr, 2023-11-17:
I'm wondering if anyone has adapted to the new Rapido 2 series, and/or the UHF version with extended air channels?  Otherwise I might hack something together

bartoszwas, 2023-11-21:
Mine Rapido 2 fits in the old Rapido 1 stl. I’m not sure does every Rapido 2 will fit but mine does…

dflemstr, 2023-11-21:
Makes sense; however in any case the UHF version is very different and would require a special part for sure.

d0m1n1qu3, 2023-11-26:
but there are two versions in the voron git one for rapido 1 and one for rapido 2 .. there must be a difference

dflemstr, 2023-12-12:
Cool, in turn I hacked together a Rapido 2 UHF version with longer cooling ducts (the back part is the same, only the front part changed)
[fillametrix-rapido-2-uhf.zip](https://github.com/sorted01/Filametrix/files/13651783/fillametrix-rapido-2-uhf.zip)
This is a Blender hack of the model you posted above, because I couldn't find a manifold version of the original parts anywhere that would let me do the mod in OpenSCAD

BrewNinja, 2023-12-31:
Did you test your version @dflemstr  ? Im looking to do the same thing.

dflemstr, 2023-12-31:
@BrewNinja yes, I am currently using my version in a printer!

d0m1n1qu3, 2023-12-31:
and here my scad with fixed stls .. is also doing his job obn my brand new voron v2.4 :-D  but only HF not UHF
[SBRapidoV2FilametrixHF.zip](https://github.com/sorted01/Filametrix/files/13801229/SBRapidoV2FilametrixHF.zip)

gordon-quad, 2024-09-14:
Can we also have Rapido v1 UHF version please?

dflemstr, 2024-12-08:
I don't think we should share the hacked versions in the repo. It is better to use the original CAD to create a properly designed version in my opinion!

JarTheHead, 2024-12-08:
ah mb i was under the assumption the second one was done with CAD

dflemstr, 2024-12-09:
Well, technically, SCAD should count as CAD, of course, but I was hoping for a `.step` based version (or Fusion 360/whatever was used to produce the `.step` files) to retain the parametric curves, etc., from the original model.

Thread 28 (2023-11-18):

Support for Vz-HextrudORT Low

kriffo88, 2023-11-18:
Hello, will it be possible to have the mod to install a Vz-HextrudORT Low?? Thank you!

sorted01, 2023-11-19:
Yes. Currently testing it as I switched to hextrudort myself.

kriffo88, 2023-11-19:
Fantastic!! Can't wait to try it, thanks again! 👍🏼

kriffo88, 2023-12-06:
> Yes. Currently testing it as I switched to hextrudort myself.

Hi, is there any news?? Thank you!😃

sorted01, 2024-01-05:
Sorry took somewhat longer. Printing test parts right now

kriffo88, 2024-01-31:
> Sorry took somewhat longer. Printing test parts right now

Hi, is there any news on the release of the file? Thank you!

siparker, 2024-02-04:
+1 for Hextudort low version also.

kriffo88, 2024-02-29:
> Sorry took somewhat longer. Printing test parts right now

Hello! No news yet? Thank you

masterviana, 2024-06-07:
Hi, is there any updated on this topic? If this can fit on Vz-HextrudORT can also FIT on sherpa mini?  Can you share your work on this so we can go forward with de design?

kriffo88, 2024-06-19:
> Hi, is there any updated on this topic? If this can fit on Vz-HextrudORT can also FIT on sherpa mini? Can you share your work on this so we can go forward with de design?

I really think there will be no updates now...

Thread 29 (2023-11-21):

Example config / readme update / slicer settings

bartoszwas, 2023-11-21:
Hey all,

Thanks for all work done in this project.

I got few questions / issues:
- can you provide an example config?
- as happy hare has macro for cutting (_MMU_CUT_TIP) which one should I use?
- what are slicer settings recommended? for now I set ramming to 0, cooling tube position to 0, but I'm not sure is it correct? If we cut filament I suppose forming tip is not necessary and its only waste of time?
- What about prime tower? Now my machine moves to prime tower, stops for half second then does the cut and goes back to prime tower. That first move to prime tower is useless but how to make it like on your vide on YouTube when on filament change it moves printhead directly to cutting position? I'm using Orca Slicer.

bartoszwas, 2023-11-21:
- happy hare says that filament got stuck in extruder - after cut filament is not retracted from sensor

bartoszwas, 2023-11-23:
So I will replay by myself to my questions, not everyone but most.

First of all I commented out Happy Hare's _MMU_CUT_TIP macro and use the one from additional.cfg

According to Slicer unchecking "Enable filament ramming" seems to doing its job in case of unnecessary move to purge tower.

Last, I've increased filament ripping after cut to 30 mm and now filament sensor is not triggered after cut.

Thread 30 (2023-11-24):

Latch is weakened - here is a stronger one.

pmaersk, 2023-11-24:
Hi
Thanks for the Filametrix. It is great. However using it, I find the latch has been weakened too much giving room to the ECAS. See picture below.

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

Below is here a modified version of the latch that is slightly enforced where the break is most likely to occur.

[[a]_latch_ecas-enforced.stl.zip](https://github.com/sorted01/Filametrix/files/13461342/a._latch_ecas-enforced.stl.zip)

Feel free to use and include as you prefer. If you give credit, then credit pmaersk/Snowmix.

EmJay276, 2023-12-14:
I also added my stronger version for the M6 motor plate, see
https://github.com/sorted01/Filametrix/pull/37

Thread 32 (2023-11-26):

mirgrate to the newer motor

d0m1n1qu3, 2023-11-26:

d0m1n1qu3, 2023-11-26:
hi could we migrate to the newer version?

here are the difference .. https://www.printables.com/de/model/555020-btt-sb2209-stealthburner-cover-updated-remix

the latch is than also more stable
see for example here
https://www.printables.com/de/model/579038-voron-clockwork2-bigtreetech-ebb-sb2209-sb2240-eca/files

d0m1n1qu3, 2023-11-26:
so we dont need this anymore ;-)
https://github.com/sorted01/Filametrix/issues/30

EmJay276, 2023-12-14:
Done via https://github.com/sorted01/Filametrix/pull/37

EmJay276, 2023-12-19:
And via https://github.com/sorted01/Filametrix/pull/40

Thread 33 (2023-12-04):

Issue with lost steps because of too much pressure while pressing the lever

seacred, 2023-12-04:
While cutting sometimes the AB Motors skip because of the high pressure applied on the lever.
Using nema 17 with 1A currently.
Did somebody noticed the same behaviour?

appleimperio, 2024-02-08:
do you manage to solve this? I'm having the same issue

seacred, 2024-02-09:
I wasn't able to solve this issue by now. i tried to reduce the cuttingmovespeed to a minimum but ist working for some cuts and suddenly it will skip. not reliable cutting over some swaps and longer prints possible by now.

slightlysketch, 2024-05-19:
so i had this issue too,
fixed it by doing a few different things

one i swapped out my 36-40 motors for some 42-40s
next i changed the run current to 1.0

if youre still skipping motors after that, its a set up issue and your plunger might be too long.
need to be very precise

seacred, 2024-06-06:
fixed it by using a setting up a gcode, which turns up the motorcurrent during cutting and resets it to default afterwards

szsong, 2024-11-25:
@seacred could you please share your gcode please?

igiannakas, 2024-12-14:
You need something like this
`[gcode_macro _SET_CUT_CURRENT]
gcode:
    M400
    SAVE_GCODE_STATE NAME=SET_CUT_CURRENT_STATE_2
    SET_TMC_CURRENT STEPPER=stepper_x CURRENT=1.9 HOLDCURRENT=1.9
    SET_TMC_CURRENT STEPPER=stepper_y CURRENT=1.9 HOLDCURRENT=1.9
    M400
    G4 P1500
    M400
    RESTORE_GCODE_STATE NAME=SET_CUT_CURRENT_STATE_2
    M400`

igiannakas, 2024-12-14:
And a similar macro for setting the print current. Set these up and hook them up to the pre unload and post load happy hare user macro extension placeholders.

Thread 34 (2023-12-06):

D2F switch does not trigger reliably on filament.

atoomnetmarc, 2023-12-06:
Hi!

I printed `SB_CW2_Main_Buddy_Cutting_with_D2F_ECAS.stl`, took a D2F Omron switch from an unused LDO klicky probe kit and used a 5.55mm 304 stainless steel ball, but the switch does not trigger reliably. When wiggling the filament sometimes the switch triggers.

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

I must be missing something obvious, do you have any pointers on what could be wrong?

atoomnetmarc, 2023-12-09:
Redesigned `SB_CW2_Main_Buddy_Cutting_with_ECAS.stp` again, now an Omron D2F-L (micro switch with lever) fits. Less resistance with this design than the previous one with the 5.55mm steel ball directly on the switch notch.

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

Going to print this full size and see how this functions.

atoomnetmarc, 2023-12-10:
When long term experience has been made I will post my modification somewhere.

Closed 2023-12-10.

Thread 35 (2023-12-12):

TAP with Magnets

ThaNeub, 2023-12-12:
Is there maybe a possibility to add the Magnet holders for Voron TAP to the toolhead mounts? Maybe the screw for fixing the cutter arm could be moved to the front, so there would be room for the magnet mounts on the back?

EmJay276, 2023-12-14:
The toolheads do not contain the Tap magnet mounts, they are located at the carriage.

ThaNeub, 2023-12-14:
The CNC Version has the magnet holders integrated in the toolhead backside: https://github.com/Chaoticlab/CNC-Tap-for-Voron/blob/master/Community%20Mods/CNC-Tap-Magnets/hot%20ends/dragon.stl

EmJay276, 2023-12-14:
I have this [CNC Tap](https://github.com/Vitalii3D-xyz/MetalTap) / [Aliexpress clone](https://www.aliexpress.com/item/1005005708018536.html) where the magnets are mounted to the CNC part, like for the original version.

My opinion: Adding the magnets to the toolhead rear breaks the basic idea of modularity for the Stealthburner.

ThaNeub, 2023-12-14:
Okay it was a Suggestion. If not possible or it breaks the idea you could close it.

EmJay276, 2023-12-14:
I am not a maintainer, @sorted01 is :)

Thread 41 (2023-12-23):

StealthOrbiter mount interfears with the cutting arm

EmJay276, 2023-12-23:
There is some interferance with the cutting arm. Thanks [@messymouse](https://github.com/messymouse) for testing!
I will create a PR and update it as soon I have some spare time to do it.

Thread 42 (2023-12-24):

Can't Find "Cutting Point on Gantry with Servo" Feature

Yanichar, 2023-12-24:
I was going through the Readme of this cool project (Project Name) and stumbled upon a mention of a "Cutting Point on Gantry with Servo." I tried to find this feature within the project's files, but no luck.

Could someone point me in the right direction or give a hint about where I might find more info about this?

murray484, 2024-01-14:
I also would like to find said file...

Thomsen1982, 2024-02-24:
Yes I am too.
Are there new information about it.

Marucci87, 2024-07-21:
I found this on thingyverse: https://www.thingiverse.com/thing:6584232 I have just printed it and will try it out within the next few days, looks like you just have to uncomment the first few lines and a few in the cutting macros in the additional.cfg. I just hope the stls I linked above will reach to my cutter....Im using the g2 extruder version. I assume if it doesnt line up I could just scale the stl for the servo mount taller or shorter.

Thomsen1982, 2024-07-21:
It looks interesting, it’s on the list for the next print 😂

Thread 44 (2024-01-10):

Mounting instruction for V6-R6 Hotend

TheMaxx2804, 2024-01-10:
Hi there,

i am missing the mounting / building instruction for the V6_R6 Hotend.
As shown in the picture the hotend is standing out some mm from the print head back and front piece.
In this case i do not know how the knife would be mounted to work correctly.

Thank you in advance for any suggestions.

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

mole6999, 2024-04-04:
I could use help woth the same problem. Has anyone figures it out yet?

protorayn, 2024-05-16:
Yes. remove the black plastic ptfe  adapter. I removed it and printed a sleeve that holds the ptfe in place for cutting.

ThunderClap86, 2024-12-19:
> > printed a sleeve that holds the ptfe in place for cutting.
>
> So the cutting knife has to be cut in length that it does stay on the silver collar and that it could not flip down that collar.
Good suggestions on both of these.

Have a STL or CAD item for the collar you made to replace the pressfit collar in the pic above?

ThunderClap86, 2024-12-19:
> Yes. remove the black plastic ptfe adapter. I removed it and printed a sleeve that holds the ptfe in place for cutting.

Guess it's you I need to be asking for the file(s) if you are willing to share.

protorayn, 2024-12-19:
I'll put it up on printables when I get home tonight

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

protorayn, 2024-12-19:
> > Yes. remove the black plastic ptfe adapter. I removed it and printed a sleeve that holds the ptfe in place for cutting.
>
> Guess it's you I need to be asking for the file(s) if you are willing to share.

https://www.printables.com/model/914674-filament-guide-sleeve-for-dragonfly-bmo

This is the sleeve I made for replacing the bowden collet.

alfadex, 2025-04-19:
@TheMaxx2804  Says the problem is here as you can see in the photo. Metal hotend is 1 mm above printed part and the cutter stop to the metal. Has somebody find any solution?

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

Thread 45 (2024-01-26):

Orbiter 2 mount not working

appleimperio, 2024-01-26:
After mounting the filametrix in my orbiter 2 with the compatible mount by emjay276 The level is not moving at all because the mount  interfere.
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

I will try this model that looks to have the clearance. https://www.printables.com/model/647601-orbiter-filametrix-mod

SaltyPaws, 2024-02-06:
I have added a pull request with 2 commits that addresses this issue, and with PG7, standard and sensor  version.

gonchogsm, 2024-05-10:
I had the same problem. I will print SaltyPaws files now. Hope they are merged because current Orbiter file is useless for filametrix

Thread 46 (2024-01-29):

Question about Voron SW

rollduck, 2024-01-29:
Good day,

I'm a Voron Switchwire owner and due to the design of this printer, I have to put a depressor unit on the z-axis instead of the y-axis and I don't know how to configure it. I've changed "variable_pin_loc_y" to "variable_pin_loc_z" but of course it doesn't work :) There is any possibility to use depressor mounted on z axis?

Thanks in advcance
Best,

Radek

appleimperio, 2024-02-08:
You just ignore the "variable_pin_loc_y" I set it up to half of the bed size just make sure the variable_pin_loc_x is correct. I'm having other issue right now but I think is skipping steps when hitting the filament.

slightlysketch, 2024-05-19:
> You just ignore the "variable_pin_loc_y" I set it up to half of the bed size just make sure the variable_pin_loc_x is correct. I'm having other issue right now but I think is skipping steps when hitting the filament.

if youre skipping steps,
make sure youre running 42-40 motors on whatever axis does the motion to hit the plunger.
second set your run current to 1.0
last dont use stealthchop (this can possibly be ignored, but i had to turn if off)

appleimperio, 2024-05-19:
@slightlysketch Thanks for your suggestion. I'm using the EREC now and it's working great.

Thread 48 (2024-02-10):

bowden contraints issue

CooperGerman, 2024-02-10:
Hi,
I'm currently using the E-RV printhead version and find myself noticing some issues with the bowden from the hexnut to hotend configuration.

The bowden cutout seems to be 4.1 mm in diameter but in my observation several bowden tubes have a tolerance to their outer diameters (in my case i have some ranging from 4.12 to 3.98).

When the bowden is not correctly imprisoned and constrained by both front and back halves, it seems that as volumetric speed rises some material builds up inside the hotend's radiator at the interface between the bowden tube and itself...

In this case, the hex nut is slightly pushed upwards (which might lead to some issues later i imagine) and printing gets harder as this build up increases.

I'm currently trying to find some solution in order to prevent this from happening that does not require proper bowden outer diameter. I was thinking about closing the canal like on picture below.

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

Do you guys see any problem with the proposed solution ? I'm going try it out and keep this issue updated as i go along.

CooperGerman, 2024-02-17:
Update 1 :
I ended up testing the following set up
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
I added a cutout for a brasse instert and resized the bowden tube to 13.6 (ish).

The bowden pointed by the red arrow is used to let the blase slide onto it and is a 2mm long ptfe tube.

I've had no issues for now, i'll let you now if any thing changes.

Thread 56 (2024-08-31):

CAD Files for EBB and D2F Options

eprouty, 2024-08-31:
I want to update the EBB and D2F options from the old motor plate, in order to support the new motor plate and M6 bowden couplers.  However, the CAD files for these old motor variants are missing.

Does anyone have these they can add? or know where I can find them?

eprouty, 2024-08-31:
@EmJay276 Do you happen to have these? Saw you had an open PR for other new motor plate STLs

EmJay276, 2024-09-03:
Did you check my changes?
https://github.com/EmJay276/ERCF_v2/blob/CW2_new_motor_plate/Recommended_Options/ERF_Filament_Cutter/README.md
I already modified the versions for the `1_Toolhead_And_Entry_Sensors`, `2_Toolhead_Sensor (EBB Board)` and `3_Entry_Sensor`

I think they were only available as STL when I modified them. So I could just do a boolean operation to remove the additional material. I attached the parts I removed from the STLs, if you need to modify other parts.
One has an Offset to fix some issues concerning the triangulation of the STL where tiny parts were left after the boolean operation.
[CW2_cutoffs_old_motor_plate.zip](https://github.com/user-attachments/files/16858855/CW2_cutoffs_old_motor_plate.zip)

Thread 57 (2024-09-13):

No body for v6 volcano hotend.

stonemandave, 2024-09-13:
If a longer version could be made for a volcano version.

stonemandave, 2024-09-13:
https://github.com/forgiven/Stealthburner-E3DV6-Volcano/blob/master/STLs/stealthburner_printhead_v6_volcano_r6_front.stl
My cad skills aren't great but this is closes I can find.

stonemandave, 2024-09-13:
https://github.com/forgiven/Stealthburner-E3DV6-Volcano/blob/master/STLs/stealthburner_printhead_v6_volcano_r6_front.stl
https://www.printables.com/model/561529-voron-stealthburner-v6volcano-toolhead-extension-m/comments
My cad skills aren't great but this is closes i can find.

stonemandave, 2024-09-14:
I made one.
https://www.printables.com/model/1006442-stealthburner-v6-volcano-filametrix-printhead

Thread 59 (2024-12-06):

Requesting missing CAD files

computernala, 2024-12-06:
Are you planning on uploading the CAD file for Cutter body small?

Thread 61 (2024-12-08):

Looking for SB_CW2_Main_Body_Cutting_with_2xD2F_ECAS CAD / Stp Datei.

kde47, 2024-12-08:
Im looking for the Stp Datei for the olr Motor Plate to optimize the holes for the heat insert. I need a hole size with 4mm. I hope you can public the Stp. Part or take an updated stl with smaller hole size.

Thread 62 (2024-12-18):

Request STP/STEP for depressor items.

ThunderClap86, 2024-12-18:
Requesting the CAD files for the Depressor Mount and Depressor to make adjustments for other printers. Planning to modify to fit on MercuryOne.1.

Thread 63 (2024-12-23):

Revo Micro Front is Currupted

irebane, 2024-12-23:
I also have checked Step and it has same issue:

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

biohazardious, 2025-01-26:
Fixed version is up on STL. Thanks to sorted01 for merge my fixed one.

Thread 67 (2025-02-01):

Question on Drilling M3 Insert and Nut

goatvirus, 2025-02-01:
Wouldn't I need to use at least a 3mm bit to remove the threads to prevent snags?  How important is this diameter for reliability?

I am trying to picture how it works.  If I cut a 1.75mm diameter filament then I would think any diameter less than two widths of the filament would allow for the remaining piece in the hot end to be reliably pushed down with the next feeding filament.

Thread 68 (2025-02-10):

Revo Voron Front overhang

qratz, 2025-02-10:
The front part for the Revo Voron has an overhang that is not really printable. The non-filametrix version prints fine at the same position.

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

ndanyluk, 2025-02-11:
@sorted01 this is the overhang we discussed in the ERCF discord #general-ercf channel back on Jan 9.  Per discussion, recommendation was to pick up the G2E-Filametrix equivalent found [here](https://github.com/IRTrail/G2E-Filametrix/blob/main/Printheads/Revo/STL/G2E%20-%20Revo%20-%20Filametrix%20-%20%20Front.stl)

@qratz I've printed this file from the other repo and it appears to work just fine for this purpose

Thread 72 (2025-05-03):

different type of cutting blade or different holder for them

toscdesign, 2025-05-03:
Hi,
It is only an idea, not really an issue.

It is very difficult to cut the type 4 plates to size.
Not everyone has a small angle grinder.

Is it possible to design a holder for the full blade or a different blade?

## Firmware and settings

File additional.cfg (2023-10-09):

#[servo cutter_gantry_servo]
#pin: PB6
#initial_angle: 180


#[gcode_macro gantry_servo_down]
#gcode:
#    SET_SERVO SERVO=cutter_gantry_servo ANGLE=55

#[gcode_macro gantry_servo_up]
#gcode:
#    SET_SERVO SERVO=cutter_gantry_servo ANGLE=180


[gcode_macro _MMU_CUT_TIP]
description: Cut filament by pressing the cutter on a pin with a horizontal movement. 

# Distance to retract prior to making the cut, this reduces wasted filament but might cause clog 
# if set too large and/or if there are gaps in the hotend assembly 
# This must be less than the distance from the nozzle to the cutter.
variable_retract_length: 33

# The location of the pin, this should be the position of the toolhead when the cutter 
# just lightly touches the pin
variable_pin_loc_x: 14
variable_pin_loc_y: 357

# The starting and end positions when making the cut
# In particular, instead of making the cut by traveling to the pin location above, 
# we leave a small safety margin along X-axis to avoid scratching on the pin when traveling
# This should also give a small distance to produce some momentum when pressing on the pin 
variable_pin_park_x_dist: 5.0

# Position of the toolhead when the cutter is fully compressed
# Should leave a small headroom (e.g., should be a bit larger than 0, or whatever xmin is) to avoid banging the toolhead or gantry
variable_pin_loc_x_compressed: 0

#  Retract length and speed after the cut so that eh cutter can go back into its origin position
variable_rip_length: 1
variable_rip_spd: 750

# Pushback of the remaining tip from the cold end into the hotend
variable_pushback_length: 0
variable_push_dwell_time: 50 # time to dwell between the pushback

# Speed related settings
# Note that if the cut speed is too fast, the steppers can lose steps
# Therefore, for a cut: 
# - We first make a fast move to accumulate some momentum and get the cut blade to the initial contact with the filament
# - We then make a slow move for the actual cut to happen 
variable_travel_spd: 7800
variable_cut_fast_move_spd: 2000
variable_cut_slow_move_spd: 500
variable_evacuate_speed: 7800
variable_cut_dwell_time: 50 # time to dwell at the cut point in ms
variable_cut_fast_move_fraction: 1.0 # fraction of the move that uses fast move 

# Safety margin for fast vs slow travel
# When traveling to the pin location, we make a safer but longer move if we closer to the pin than this specified margin
# Usually setting these to the size of the toolhead (plus a small margin) should be good enough 
variable_safe_margin_x: 30
variable_safe_margin_y: 30

# Whether or not to make a second cut
# The goal of the second cut is to avoid filament adding friction to the blade causing the lever unable to decompress
# If set to a positive value, we first retract this amount, make the second cut, then extrude back
# Set to 0 to disable to second cut
# You should only enable this if you cannot get the lever to reliabily decompress.
variable_second_cut_retract_length: 0

# Whether to eject the filament at the end
variable_final_eject: 0

# Currently ERCF software assumes that tip forming move always moves the extruder (and consequently the encoder)
# Ideally, we should bring formal support of filament cutters to the ERCF software
# In the short term, we perform a "hack" where we wiggle the extruder a little after cutting, 
# if the extruder did not make enough movement during the filament cutting phase.
variable_extruder_minimum_movement: 0 # the minimum extruder movement required for this tip forming move, this depends on the minimum distance that the encoder can reliably detect
                                      # setting it to a lower value requires the ERCF encoder to be more sensitive.
variable_extruder_wiggle_length: 10 # the length to retract -> extrude during a wiggle, this needs to be large enough for the encoder to detect the movement
variable_extruder_wiggle_repeat: 3 # number of repeats for the wiggle

# Optionally move to location immediately after making the cut
#variable_x_after_toolchange: -1000
#variable_y_after_toolchange: -1000

variable_output_park_pos: 37.5 #  this should be set to the distance from the nozzle tip to the blade for filametrix type cutter

gcode:
    {% set RETRACT_LENGTH = params.RETRACT_LENGTH | default(printer['gcode_macro _MMU_CUT_TIP']['retract_length']) | float %}
    {% set PUSHBACK_LENGTH = params.PUSHBACK_LENGTH | default(printer['gcode_macro _MMU_CUT_TIP']['pushback_length']) | float %}
    {% set FINAL_EJECT = params.FINAL_EJECT | default(printer['gcode_macro _MMU_CUT_TIP']['final_eject'], True) | int %}
    {% set current_loc_x = printer.gcode_move.gcode_position.x %}
    {% set current_loc_y = printer.gcode_move.gcode_position.y %}
    {% set push_dwell_time = printer['gcode_macro _MMU_CUT_TIP']['push_dwell_time'] | float %}

    SAVE_GCODE_STATE NAME=_MMU_CUT_TIP_state
    
    {% if ("x" not in printer.toolhead.homed_axes) or ("y" not in printer.toolhead.homed_axes) %}
        G28 X Y
    {% endif %}

    {% set prev_pa = printer.extruder.pressure_advance %}
    SET_PRESSURE_ADVANCE ADVANCE=0 # temporaily disable PA

    {% set pin_park_x_loc = pin_loc_x + pin_park_x_dist %}
    {% set pin_park_y_loc = pin_loc_y %}
    {% set _extruder_moved_dist = 0 %}

    M83 # relative extrusion
    {% if RETRACT_LENGTH > 0 %}
        G1 E-{RETRACT_LENGTH} F3000 # retract to save filament waste
        {% set _extruder_moved_dist = _extruder_moved_dist + RETRACT_LENGTH %}
    {% endif %}

#    gantry_servo_up
    
    G90 # absolute positioning
    _MOVE_TO_CUTTER_PIN PIN_PARK_X_LOC={pin_park_x_loc} PIN_PARK_Y_LOC={pin_park_y_loc}

#    gantry_servo_down
    
    # Make the main cut 
    _DO_CUT_MOTION PIN_PARK_X_LOC={pin_park_x_loc} RIP_LENGTH={rip_length}
    {% set _extruder_moved_dist = _extruder_moved_dist + rip_length %}
    
    # Optional secondary cut to help decompressing the lever
    {% if second_cut_retract_length > 0 %}
        G1 E-{second_cut_retract_length} F3000
        _DO_CUT_MOTION PIN_PARK_X_LOC={pin_park_x_loc} RIP_LENGTH=-1
        G1 E{second_cut_retract_length} F3000
    {% endif %}

#    gantry_servo_up


    # pushback of the tip residual into the hotend
    {% if PUSHBACK_LENGTH > 0 %} 
        G1 E{PUSHBACK_LENGTH} F1000 
#        G4 P{push_dwell_time}
#        G1 E-{PUSHBACK_LENGTH} F1000
        {% set _extruder_moved_dist = _extruder_moved_dist - PUSHBACK_LENGTH %}
    {% endif %}
    
    {% if FINAL_EJECT == 1 %}
        G1 E-80 F3000
        {% set _extruder_moved_dist = _extruder_moved_dist + 80 %}
    {% endif %}

    {% if _extruder_moved_dist < extruder_minimum_movement %}
        # make some wiggle moves so that the encoder catch them
        {% for _ in range(extruder_wiggle_repeat) %}
            G1 E-{extruder_wiggle_length} F3000
            G1 E{extruder_wiggle_length} F3000
        {% endfor %}
    {% endif %}

    SET_PRESSURE_ADVANCE ADVANCE={prev_pa} # restore PA

#    {% set move_to_next_loc = ((x_after_toolchange != -1000) and (y_after_toolchange != -1000)) | int %}
#    {% if move_to_next_loc %}
#        G1 X{x_after_toolchange} Y{y_after_toolchange} F{travel_spd}
#    {% endif %}

 #   _SET_LOC_AFTER_TOOLCHANGE # clears the location
    RESTORE_GCODE_STATE NAME=_MMU_CUT_TIP_state MOVE_SPEED=250


#[gcode_macro _SET_LOC_AFTER_TOOLCHANGE]
#description: Set the location to travel after making a cut
#gcode:
#    # Note that we use an extremely negative number to represent that we not moving anywhere afte toolchange
#    {% set x_after_toolchange = params.X | default (-1000) | float %}
#    {% set y_after_toolchange = params.Y | default (-1000) | float %}
#    SET_GCODE_VARIABLE macro=_MMU_CUT_TIP variable=x_after_toolchange value={x_after_toolchange}
#    SET_GCODE_VARIABLE macro=_MMU_CUT_TIP variable=y_after_toolchange value={y_after_toolchange}


[gcode_macro _MOVE_TO_CUTTER_PIN]
description: helper to move the toolhead to the target pin in either safe or faster way, depending on toolhead clearance.
gcode:
    {% set safe_margin_x = printer['gcode_macro _MMU_CUT_TIP']['safe_margin_x'] | float %}
    {% set safe_margin_y = printer['gcode_macro _MMU_CUT_TIP']['safe_margin_y'] | float %}
    {% set travel_spd = printer['gcode_macro _MMU_CUT_TIP']['travel_spd'] | float %}
    {% set pin_park_x_loc = params.PIN_PARK_X_LOC | float %}
    {% set pin_park_y_loc = params.PIN_PARK_Y_LOC | float %}

    G90 # absolute positioning
    {% if ((printer.gcode_move.gcode_position.x - pin_park_x_loc) | abs < safe_margin_x) or ((printer.gcode_move.gcode_position.y - pin_park_y_loc | float) | abs < safe_margin_y) %}
        # Make a safe but slower travel move
        G1 X{pin_park_x_loc} F{travel_spd}
        G1 Y{pin_park_y_loc} F{travel_spd}
    {% else %}
        G1 X{pin_park_x_loc} Y{pin_park_y_loc} F{travel_spd}
    {% endif %}
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

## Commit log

2023-05-13 Added first assembly instructions
2023-05-19 Created CAD Folder
    [test.step]
2023-05-19 CAD / STEP Files added
    [Cutting_Arm.stp, Knife_holder.stp, SB_CW2_Main_Buddy_Cutting_with_ECAS.stp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]
2023-05-31 Create Bambu Toolhead
2023-06-01 Remixed for Voron Revo Hotend
    [SB_RevoVoron_back.stl, SB_RevoVoron_back.stp]
2023-06-04 add my implementation of cut macro
    [ercf_additional.cfg]
2023-06-05 updates and fixes
    [ercf_additional.cfg]
2023-06-05 change all semicolon to # per user feedback
    [ercf_additional.cfg]
2023-06-20 moved to Revo folder
    [SB_RevoVoron_back.stl]
2023-09-08 Create Joined SB_Bambu_cutting_Printhead_front.stl
    Fixed 2 piece bambu print head front
2023-09-10 Create Bambu Adapter M5 nut.stl
    Designed the adapter to use a standard M5 nut and 5mm brass heat sets.
    [Bambu Adapter M5 nut.stl]
2023-09-10 Update ercf_additional.cfg
    Fixed cutting gcode
    [ercf_additional.cfg]
2023-09-12 Update ercf_additional.cfg
    Updated macro to work with HHv2
    [ercf_additional.cfg]
2023-09-15 Add V6 R6 Printhead
    [SB_V6_R6_cutting_printhead_back.step, SB_V6_R6_cutting_printhead_back.stl]
2023-09-16 Fix STLs
    [SB_V6_R6_cutting_printhead_back.stl]
2023-09-16 Fixed and updated code
    Changed the way gcode save states being handled.
    [mmu_additional.cfg]
2023-11-09 Spring details added
2023-12-13 Add Phaetus Dragon UHF and Phaetus Dragon UHF mini toolhead
    [Knife_holder_Dragon_UHF.stl, Knife_holder_Dragon_UHF.stp, SB_Dragon_UHF_cutting_TH_Rear.stl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]
2023-12-14 Main Body for new CW2 motor plate with ECAS and M6 fitting
    Addionally, add the part that was cut off to adapt the other main bodys
    [SB_CW2_cutoff_new.stp, SB_CW2_new_motor_plate_Main_Buddy_Cutting_with_ECAS.stl, SB_CW2_new_motor_plate_Main_Buddy_Cutting_with_ECAS.stp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]
2023-12-14 Add more clearance
    [Knife_holder_Dragon_UHF.stl, Knife_holder_Dragon_UHF.stp]
2023-12-14 Rename file
    [SB_CW2_cutoff_new_motor_plate.stp]
2023-12-14 Latch for M6 motor plate
    Stronger than the ECAS version
    [[a]_latch_M6.stl, [a]_latch_M6.stp]
2023-12-14 Split files by old and new motor plate
    [SB_CW2_Main_Buddy_Cutting_with_2xD2F_ECAS fix Rev1.stl, SB_CW2_Main_Buddy_Cutting_with_D2F_ECAS.stl, SB_CW2_Main_Buddy_Cutting_with_ECAS.stl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]
2023-12-19 Add StealthOrbiter extruder support
    [ORBITERMOUNT_STANDARD_PG7_V2_Cutting.stl, ORBITERMOUNT_STANDARD_PG7_V2_Cutting.stp]
2024-02-06 Fix for issue #45, lever are does not close and adding standard and sensor version for StealthOrbiter Toolhead.
    [ORBITERMOUNT_No_Sensor_V3_Cutting v2.stl.3mf, ORBITERMOUNT_No_Sensor_V3_Cutting v2.stl.f3d, ORBITERMOUNT_No_Sensor_V3_Cutting v2.stl.step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]
2024-02-06 Fix for issue #45, PG7 version
    [Cutter body small.obj, ORBITERMOUNT_STANDARD_PG7_V2_Cutting.stl, ORBITERMOUNT_STANDARD_PG7_V2_Cutting.stp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]
2024-04-02 add new_motor_plate support for latch_ecas
    add new_motor_plate support for latch_ecas
    [[a]_latch_ecas-new_motor.STL, [a]_latch_ecas.STEP]
2024-04-19 Add files via upload
    Cable door for CW2 version with ECAS
    [SB_CW2_FILAMETRIX_ECAS_CABLEDOOR.stl]
2024-12-08 Added Revo Micro version
    [SB_RevoMicro_back.stl]
2025-01-20 Fix for Revo Micro
    [SB_RevoMicro_back.stl]
